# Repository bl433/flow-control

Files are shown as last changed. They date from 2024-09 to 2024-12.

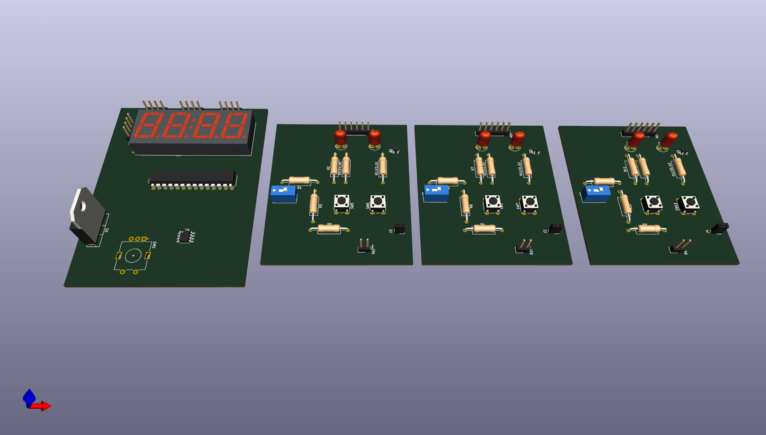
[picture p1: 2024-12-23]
hardware/kicad/flowcontrol_render.png

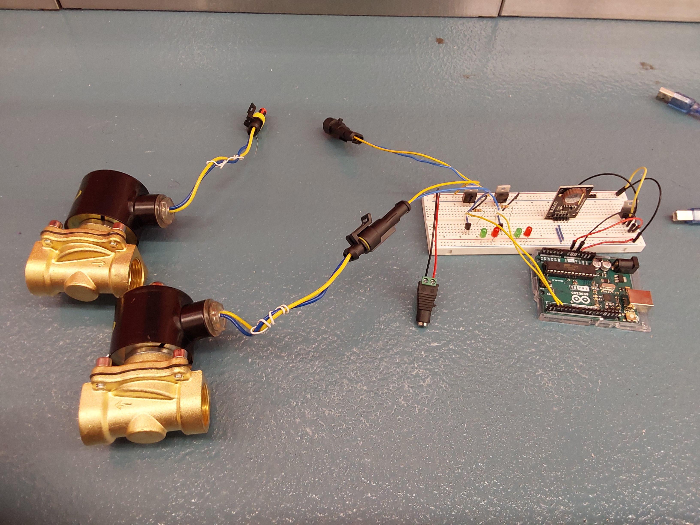
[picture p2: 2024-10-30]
documentation/Breadboarding.jpg

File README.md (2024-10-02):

# flow-control
Solenoid valve manager with PWM-styled energizing, master control, and possible flow rate feedback.
- Nozzle sizes are 3/4", meant for standard purpose garden hoses.
- Intended to be powered by a 12V 2A power supply.
- Solenoids are connected to the bottom of the valve manager through a 2-pin socket.

<b>This repository is intended for the NJIT ECET-430 course.</b>

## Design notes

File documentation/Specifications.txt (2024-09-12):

Suggested components:
 - resistors
 - MOSFET transistors or relays
 - indicator LEDs
 - 5V voltage regulators

Main Switch:
 - single-pole, single-throw
 - final decision: entire solenoid valve is off if this is off

Potentiometer Knob:
 - turnable, variable resistor
 - delays the solenoid valve for a variable amount of hours depending how far the potentiometer turns
 - solenoid valve is allowed a specific duty cycle to conserve water
 - turning the knob at maximum should allow the solenoid to open every 24 hours,
 - while turning the knob at minimum should allow the solenoid to open every 1 hours.
 - another knob can be used to decide how LONG the solenoid valve opens.

Solenoid Valve:
 - handles liquid transfer based on Main Switch ~~and Potentiometer Knob~~
 - 3/4in diameter
 - 12V, 2A input
 ~ 30 min active time until it begins to overheat

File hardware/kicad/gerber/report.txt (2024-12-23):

Warning: Width correction constrained.  The width correction value must be in the range of [0.000001 mm; 0.199999 mm] for the current design rules.
Plotted to 'H:\GitHub\flow-control\hardware\kicad\gerber\flowcontrol_BL-F_Cu.gbr'.
Plotted to 'H:\GitHub\flow-control\hardware\kicad\gerber\flowcontrol_BL-In1_Cu.gbr'.
Plotted to 'H:\GitHub\flow-control\hardware\kicad\gerber\flowcontrol_BL-In2_Cu.gbr'.
Plotted to 'H:\GitHub\flow-control\hardware\kicad\gerber\flowcontrol_BL-B_Cu.gbr'.
Plotted to 'H:\GitHub\flow-control\hardware\kicad\gerber\flowcontrol_BL-F_Paste.gbr'.
Plotted to 'H:\GitHub\flow-control\hardware\kicad\gerber\flowcontrol_BL-B_Paste.gbr'.
Plotted to 'H:\GitHub\flow-control\hardware\kicad\gerber\flowcontrol_BL-F_Silkscreen.gbr'.
Plotted to 'H:\GitHub\flow-control\hardware\kicad\gerber\flowcontrol_BL-B_Silkscreen.gbr'.
Plotted to 'H:\GitHub\flow-control\hardware\kicad\gerber\flowcontrol_BL-F_Mask.gbr'.
Plotted to 'H:\GitHub\flow-control\hardware\kicad\gerber\flowcontrol_BL-B_Mask.gbr'.
Plotted to 'H:\GitHub\flow-control\hardware\kicad\gerber\flowcontrol_BL-Edge_Cuts.gbr'.
Created Gerber job file 'H:\GitHub\flow-control\hardware\kicad\gerber\flowcontrol_BL-job.gbrjob'.
Info: Done.

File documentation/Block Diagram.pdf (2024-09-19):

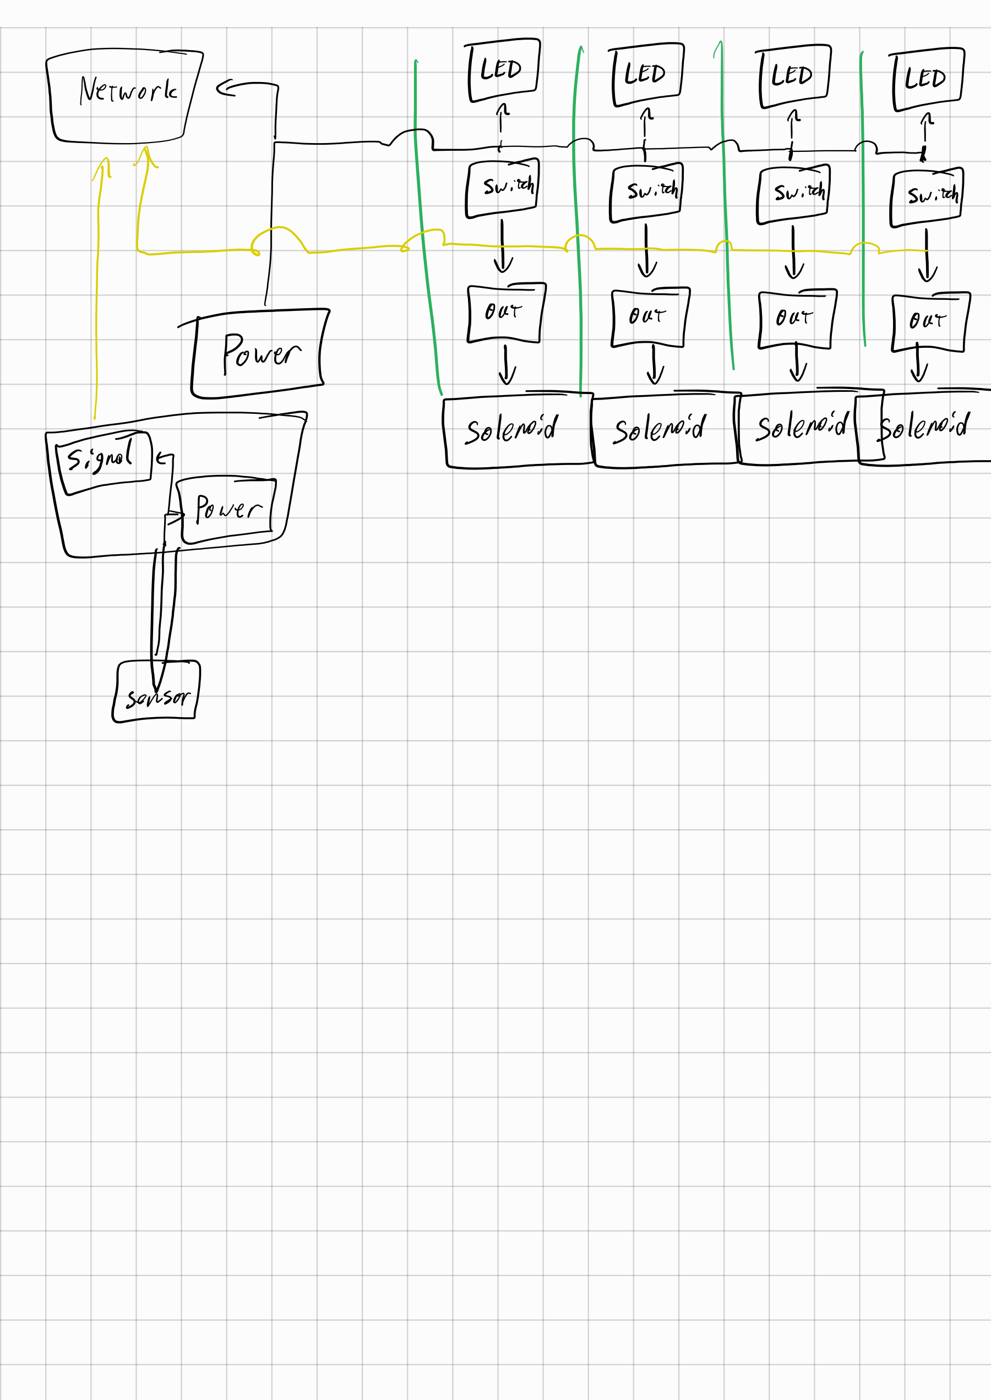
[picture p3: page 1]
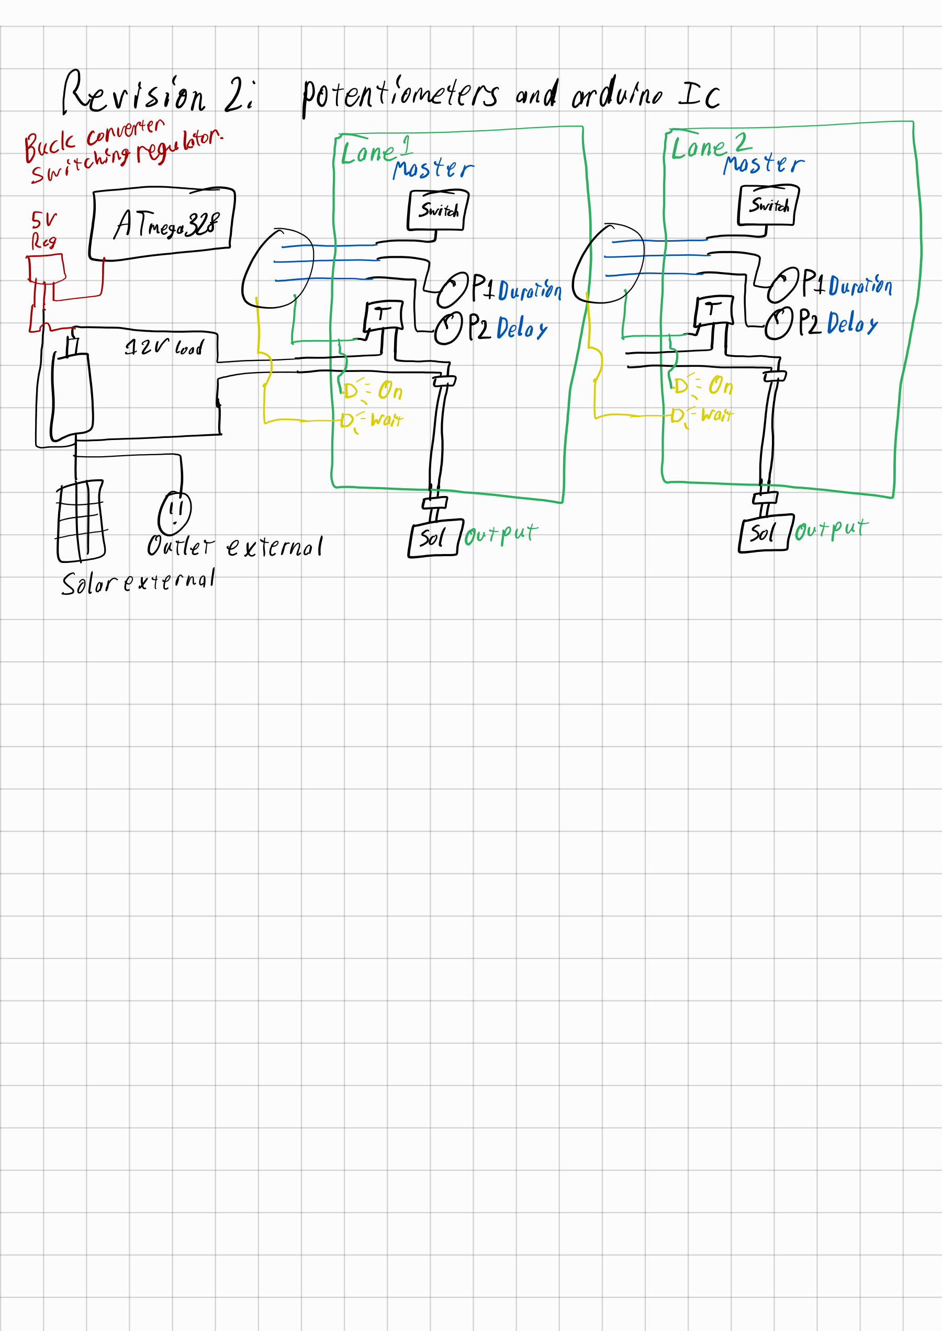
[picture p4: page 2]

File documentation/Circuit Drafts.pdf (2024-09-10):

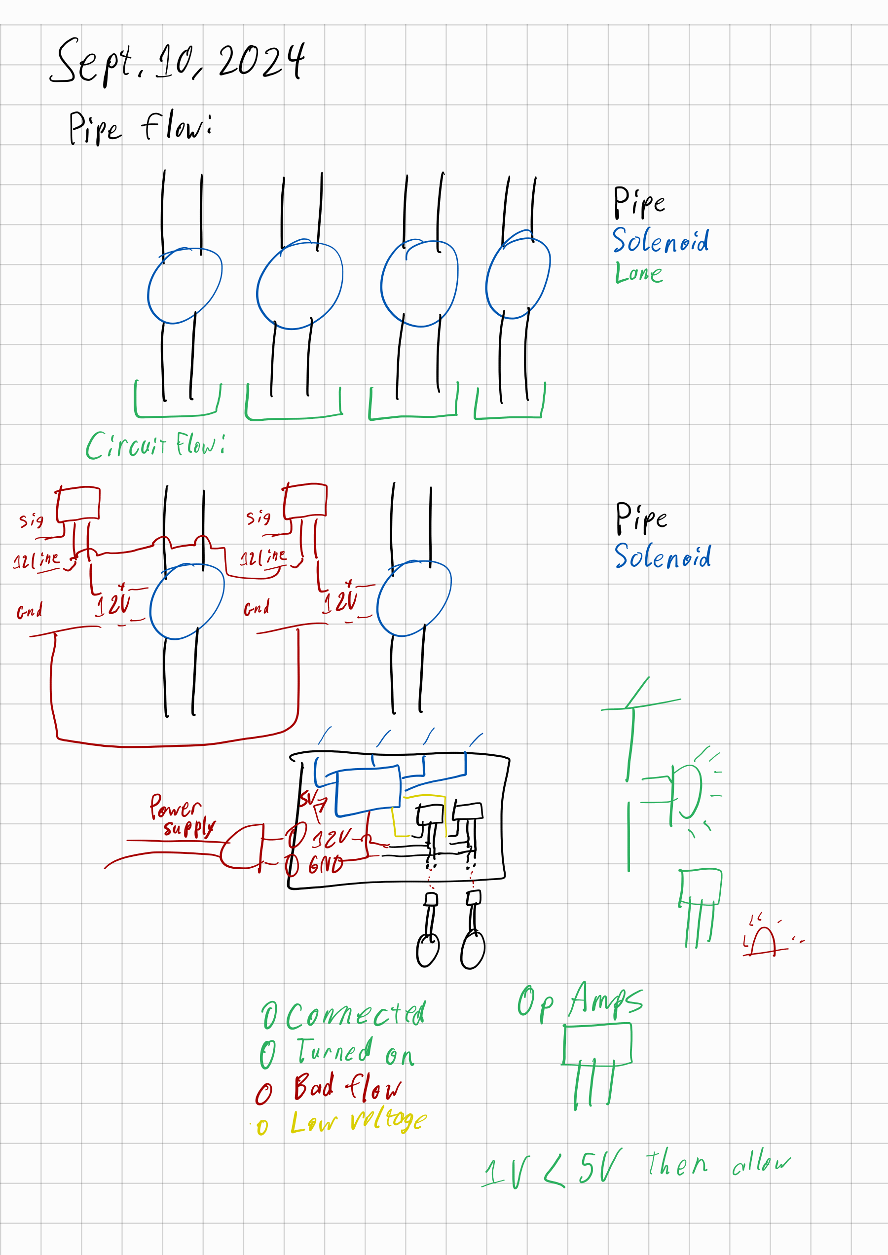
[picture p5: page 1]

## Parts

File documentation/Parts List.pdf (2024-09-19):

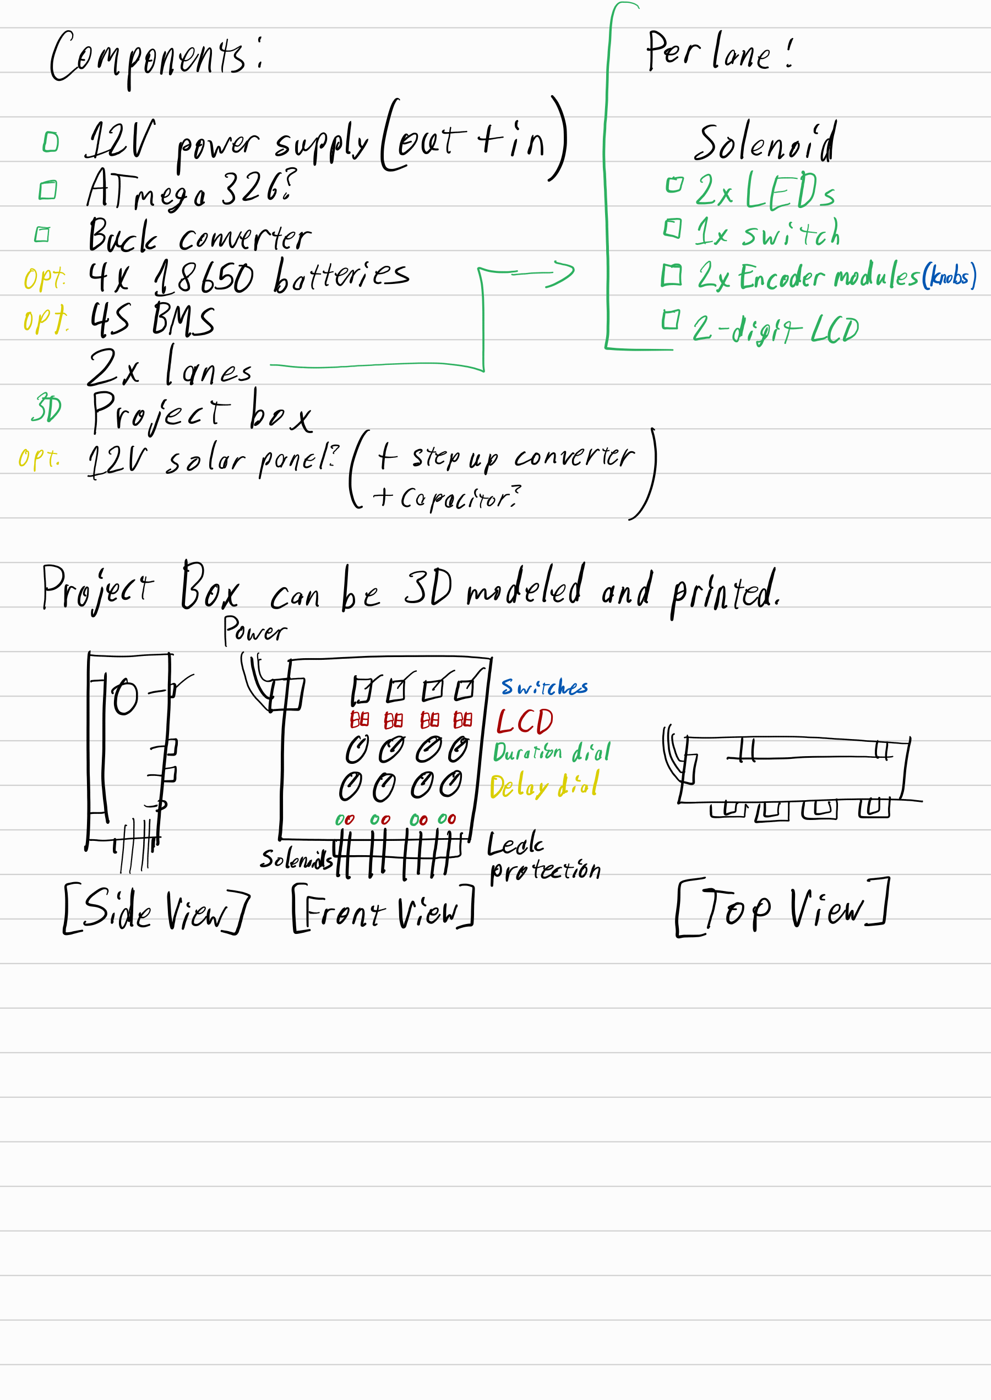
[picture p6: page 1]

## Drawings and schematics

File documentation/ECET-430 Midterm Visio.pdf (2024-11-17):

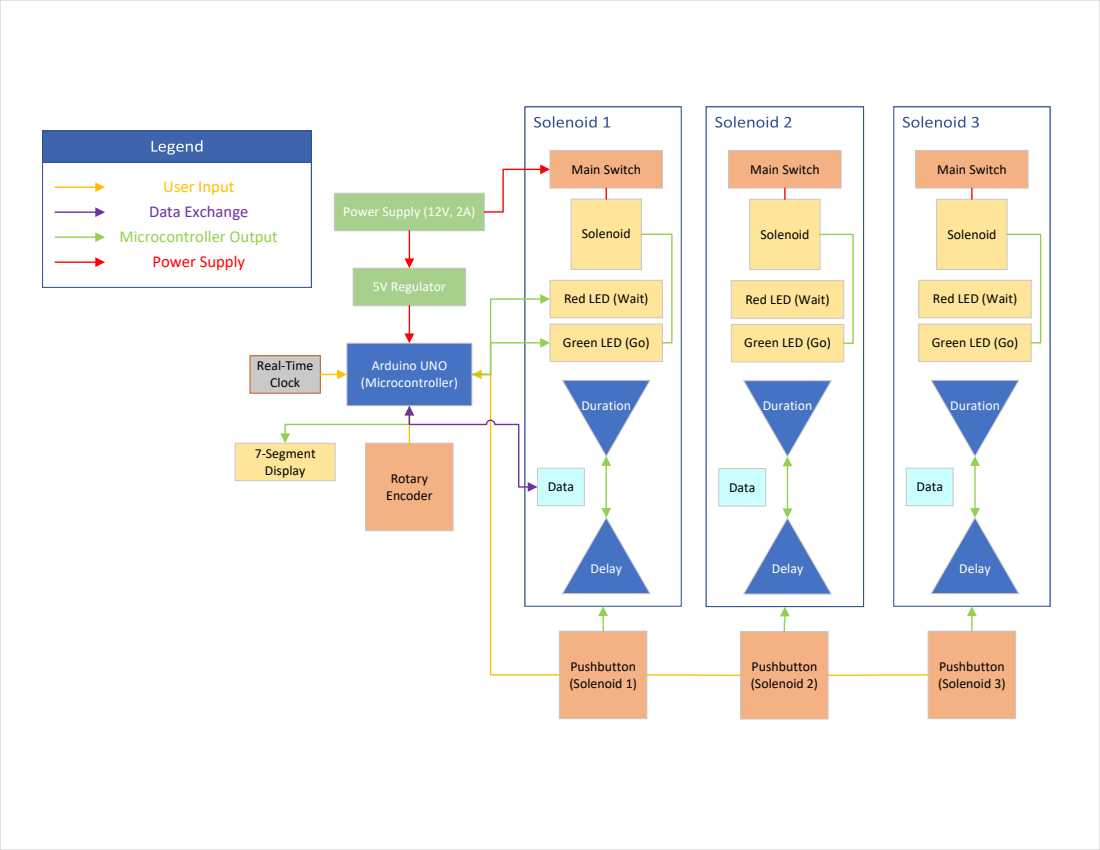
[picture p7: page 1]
Power Supply (12V, 2A); Arduino UNO (Microcontroller); Pushbutton (Solenoid 1); Delay; Duration; Rotary Encoder; Solenoid; 5V Regulator; 7-Segment Display; Data; Real-Time Clock; Pushbutton (Solenoid 2); Pushbutton (Solenoid 3); User Input Data Exchange; Microcontroller Output; Power Supply; Main Switch

Red LED (Wait)

Green LED (Go)

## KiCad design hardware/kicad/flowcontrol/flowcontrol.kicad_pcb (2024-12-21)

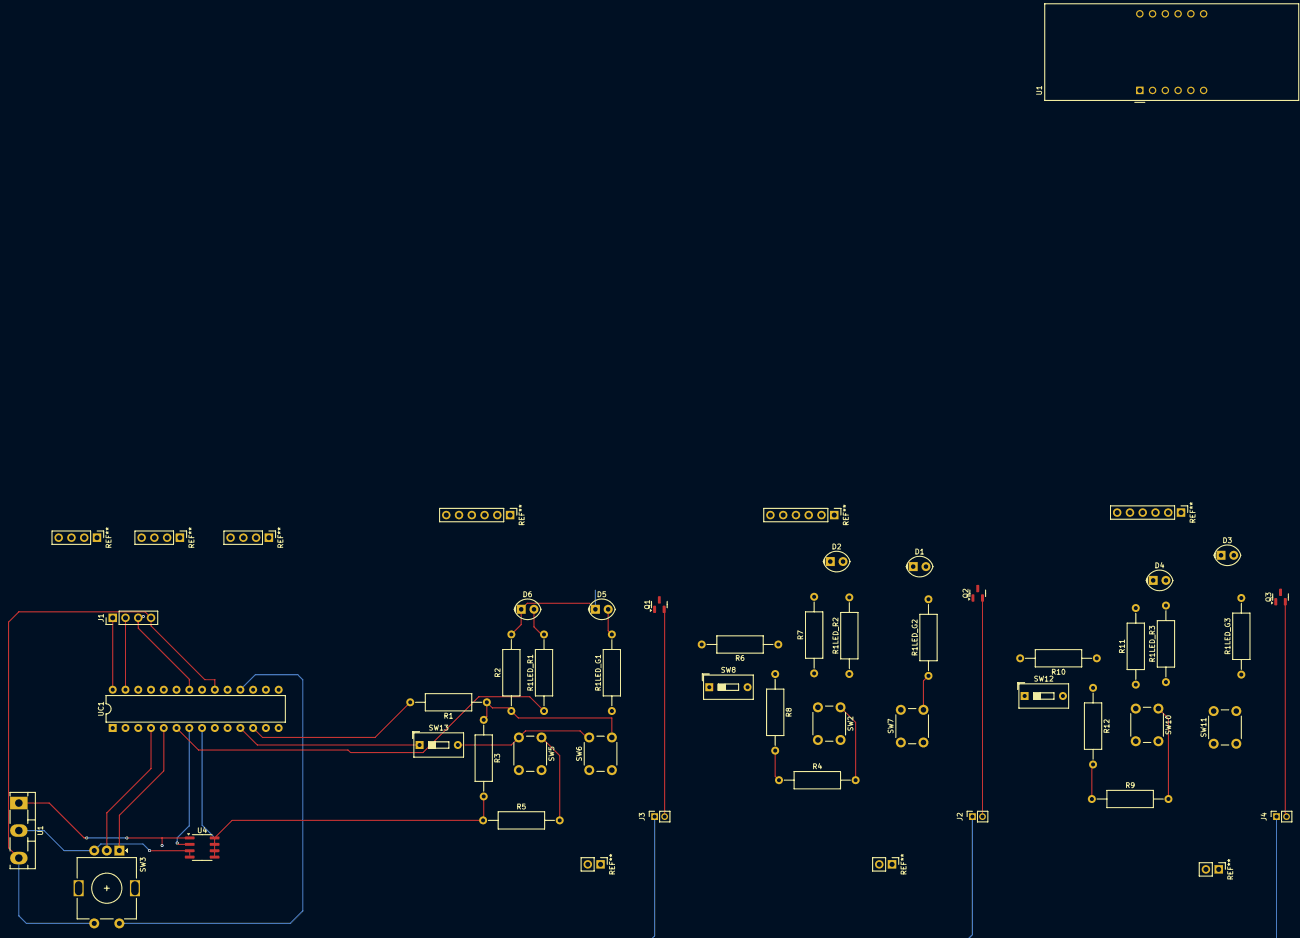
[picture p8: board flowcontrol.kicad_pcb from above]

Board: 2 copper layers, 45 parts (0 on the bottom side), 33 nets.

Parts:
D1, D3, D5: SOL1_GRN; LED_Oval_W5.2mm_H3.8mm
D2, D4, D6: SOL1_RED; LED_Oval_W5.2mm_H3.8mm
J1: 4-digit I2C Display; PinHeader_1x04_P2.54mm_Vertical
J2, J3, J4: SOL1_PORT; PinSocket_1x02_P2.00mm_Vertical
Q1, Q2, Q3: SOL1_NFET; SOT-23
R1, R6, R10: 100O; R_Axial_DIN0309_L9.0mm_D3.2mm_P15.24mm_Horizontal
R1LED_G1, R1LED_G2, R1LED_G3: 220; R_Axial_DIN0309_L9.0mm_D3.2mm_P15.24mm_Horizontal
R1LED_R1, R1LED_R2, R1LED_R3: R; R_Axial_DIN0309_L9.0mm_D3.2mm_P15.24mm_Horizontal
R2, R4, R5, R7, R9, R11: 1kO; R_Axial_DIN0309_L9.0mm_D3.2mm_P15.24mm_Horizontal
R3, R8, R12: 100; R_Axial_DIN0309_L9.0mm_D3.2mm_P15.24mm_Horizontal
SW2, SW5, SW10: BUTTON_CONFIG; SW_PUSH_6mm_mod
SW3: DIAL; RotaryEncoder_Vertical_H20mm
SW6, SW7, SW11: BUTTON_FORCE; SW_PUSH_6mm_mod
SW8, SW12, SW13: SWITCH_MAIN; SW_DIP_SPSTx01_Slide_9.78x4.72mm_W7.62mm_P2.54mm
U1: SOL1_DISP; CA56-12SRWA
U1#2: 5V Regulator; TO-218-3_Vertical
U4: XL1509-3.3; SOIC-8_3.9x4.9mm_P1.27mm
UC1: ATmega328-P; DIP-28_W7.62mm

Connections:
/Input Display/12V_R: J2.1, J3.1, J4.1, U1#2.1 (IN), U4.1 (VIN)
/Input Display/CLOCK: SW3.C, UC1.4 (PD2)
/Input Display/DT: SW3.A, UC1.5 (PD3)
/Input Display/SCL: J1.1, UC1.28 (PC5)
/Input Display/SDA: J1.2, UC1.27 (PC4)
/Input Display/SWITCH: SW3.S2, UC1.18 (PB4)
/Input Display/VCC_E: J1.4, SW2.4, SW3.S1, SW5.4, SW6.1, SW7.1, SW8.2 (B), SW10.4, SW11.1, SW12.2 (B), SW13.2 (B), U1#2.3 (OUT), UC1.20 (AVCC)
/Microcontroller/SOL1_MAIN: SW13.1 (A), UC1.11 (PD5)
/Microcontroller/SOL1_OUT: R1.2, UC1.12 (PD6)
/Microcontroller/SOL1_SEL: R5.2, SW5.3, UC1.13 (PD7)
/Microcontroller/SOL1_WAIT: R1LED_R1.1, UC1.6 (PD4)
/Microcontroller/SOL2_MAIN: SW8.1 (A), UC1.14 (PB0)
/Microcontroller/SOL2_OUT: R6.2, UC1.15 (PB1)
/Microcontroller/SOL2_SEL: R4.2, SW2.3, UC1.17 (PB3)
/Microcontroller/SOL2_WAIT: R1LED_R2.1, UC1.16 (PB2)
/Microcontroller/SOL3_MAIN: SW12.1 (A), UC1.23 (PC0)
/Microcontroller/SOL3_OUT: R10.2, UC1.24 (PC1)
/Microcontroller/SOL3_SEL: R9.2, SW10.3, UC1.26 (PC3)
/Microcontroller/SOL3_WAIT: R1LED_R3.1, UC1.25 (PC2)
GND: D1.1 (K), D2.1 (K), D3.1 (K), D4.1 (K), D5.1 (K), D6.1 (K), J1.3, Q1.1 (D), Q1.3 (G), Q2.1 (D), Q2.3 (G), Q3.1 (D), Q3.3 (G), R2.2, R3.2, R4.1, R5.1, R7.2, R8.2, R9.1, R11.2, R12.2, SW3.B, U1#2.2 (GND), U4.3 (FB), U4.4 (~EN), U4.5 (GND), U4.6 (GND), U4.7 (GND), U4.8 (GND), UC1.8 (GND), UC1.22 (GND)
unnamed: D1.2 (A), R1LED_G2.2
unnamed: D2.2 (A), R1LED_R2.2
unnamed: D3.2 (A), R1LED_G3.2
unnamed: D4.2 (A), R1LED_R3.2
unnamed: D5.2 (A), R1LED_G1.2
unnamed: D6.2 (A), R1LED_R1.2
unnamed: J2.2, Q2.2 (S)
unnamed: J3.2, Q1.2 (S)
unnamed: J4.2, Q3.2 (S)
unnamed: R1.1, R1LED_G1.1, R2.1, R3.1, SW6.2
unnamed: R1LED_G2.1, R6.1, R7.1, R8.1, SW7.2
unnamed: R1LED_G3.1, R10.1, R11.1, R12.1, SW11.2
unnamed: U4.2 (OUT), UC1.7 (VCC)

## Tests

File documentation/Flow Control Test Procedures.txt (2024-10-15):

Bruce Le's Test Procedures for the Flow Control manager [October 15th, 2024]:

 [Startup process:]
  - The product is energized as soon as it's plugged in. To ensure the product is working afterwards, it should light up all the RED (delay) LEDs for a few seconds.
  - The purpose of this test is to verify that the product will work as intended with some kind of "sanity test." If it does not have its LEDs light up for a few seconds, then its instructions were incorrectly uploaded, or some components may have failed.

 [Manual activation:]
  - Press the duration encoder knob to manually enable the solenoid, independent of the cycle.
  - This can be ideal for sampling where the water will go when connecting it to a pipe network.
  - The purpose of this test is to verify that the solenoids themselves are working as intended, meaning the solenoids can activate as intended when the delay cycle passes.

 [Template activation cycle:]
  - A small-scale test instance. On a duration of 30 seconds, and a delay of 60 seconds, the solenoid should wait 60 seconds before opening for 30 seconds. This cycle must constantly repeat.
  - During this time, the red LED must be blinking, showing that the solenoid is currently on its delay cycle, then the green LED must be solid for 30 seconds, showing that it's then on an active cycle.
  - The purpose of this test is to verify that the delay and duration cycles work to the user's intent. The duration and delay timers can be increased until it can be considered comfortable to perform a 10-hour delay or greater.

 [Adjusting individual settings:]
  - Each of the two encoder knobs can be turned to change the settings for the respective solenoid. The settings must be independent for each solenoid.
   [IE. Solenoid 1 has a duration of 5 minutes 05:00 and a delay of 20 hours 20:00
        Solenoid 2 has a duration of 10 minutes 10:00 and a delay of 12 hours 12:00]
  - The purpose of this test is to verify that each solenoid will have their own individual settings, as well as opening and closing at different intervals as per the solenoid's provided duration and delay.
  - A solenoid should not follow the duration or delay that is assigned to another solenoid.

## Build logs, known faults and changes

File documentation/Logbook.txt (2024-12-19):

flow-control (12V, 2A each) logbook [Fall Semester, 2024]
Bruce Le, mohammad, Felipe
September 3rd, 2024
 - Initiated project, proposed solenoid valve manager
 - Placed order for two solenoid valves
 - Set up github directories
September 5th, 2024
 - Sorted github directories
<<<<<<< HEAD
September 10th, 2024
 - Drawn block diagram and circuit drafts
 - Changed up specifications
  - Changed from partially open solenoid valves to cyclically open solenoid valves
September 12th, 2024
 - Decided to integrate Arduino
  - Requires the Arduino code and USB to serial conversion
=======
September 12th, 2024
 - Added parts list

=======
October 17th, 2024
 - Test operated solenoids through an Arduino blink function
October 28th, 2024
 - Assembled solderless breadboard circuit and installed waterproof cables for solenoids
November 13th, 2024
- Test out the project's functions prior to the presentation midterm.
December 12th, 2024
- Worked on the module board and mother board. Soldered them to be ready to present on 12/19.

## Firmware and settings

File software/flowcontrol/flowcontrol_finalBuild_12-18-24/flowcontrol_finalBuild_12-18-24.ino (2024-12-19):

/* ECET-430 Midterm - Flow Control Prototype
  We want this to exhibit the basics of what we're doing.
  Eventually we'll evolve this to two solenoids, but three and four is a pipe dream unless we can expand the IO pins.
  Each solenoid will be backed with a master switch.
  
*/

//================//
// PIN DEFINITION //
//================//

// Define rotary encoder pins
#define ENC_A 2
#define ENC_B 3
#define ENC_SW 12
// MAIN - Main decision switch. Solenoid will not flow or count down if not receiving 5v. (off)
// OUT - Output valve control. Linked to the green LED.
// WAIT - Hold visual. Linked to the red LED.
// SW_SEL - Pushbutton to select solenoid for configuration. Push once for Delay, push twice for Duration.
// SW_FORCE - Pushbutton to forcefully enable SOL1_OUT. This doesn't even need to exist and can be linked to a 5V.
#define SOL1_MAIN 5
#define SOL1_OUT 6
#define SOL1_WAIT 4
#define SOL1_SW_SEL 7
//#define SOL1_SW_FORCE 11
#define SOL2_MAIN 8
#define SOL2_OUT 9
#define SOL2_WAIT 10
#define SOL2_SW_SEL 11
// It's impossible to expand to the fourth solenoid with the current microcontroller unless there's a way to expand the pins.
// We COULD squeeze one, pins 14, 15, 16, 17 for SOL3. Not SOL4 though. Three might as well be our absolute maximum.
// There are ways. An 8-pin expansion board would be ideal for this matter, but ends up relying on I2C communications, SDA, and SCL.
#define SOL3_MAIN 14
#define SOL3_OUT 15
#define SOL3_WAIT 16
#define SOL3_SW_SEL 17

#define HOUR_CONVERT 60
#include "HT16K33.h"

unsigned long _lastIncReadTime = micros(); 
unsigned long _lastDecReadTime = micros(); 
int _pauseLength = 25000;
int _fastIncrement = 10;
int _delaysPerSecond = 10;
int delayCount = 0;
#define ONE_SECOND 1000

//======================//
// VARIABLE DEFINITIONS //
//======================//

// Solenoids based on the manual switch. MUST default to false if the switch is damaged.
bool solenoidEnabled[] = {false, false, false};
// Solenoids with individual duration counters, in seconds.
int solenoidDuration[] = {0, 0, 0};
// Solenoids with individual delay counters, in minutes.
// Neither the delay or duration counters can go below 0.
int solenoidDelay[] = {1, 2, 3};
// Current solenoid. Ranges from 1 to 3.
int solenoidSelect = 1;
// Editing what part of that solenoid. 1 for delay, 2 for duration.
int solenoidEditing = 1;
// Counters. These go down one for every minute.
//  They'd be normally what, 60, 120, 180 minutes? Setting these to 1, 2, and 3 is just for the presentation tomorrow.
int solenoidCounters[] = {1, 2, 3};
int secondCounter = 0;
int blinkState = LOW;

struct HrAndMin {
  int16_t hours;
  int16_t minutes;
};

// Constraints - if the counters ever go past these numbers, the code will force the value to the cap values.
#define SOL_MAX 1800
#define SOL_MIN 0

// This counter will be useful. Basically when you select a solenoid...
//  LOAD the DELAY to the COUNTER and UPDATE the value.
//  Make it display DELAY (DEly) for a second, then the actual counter itself.
//  Adjust the COUNTER to what you desire.
//  Press the encoder switch to SAVE the COUNTER to the DELAY.
//  Make the LCD say SET or something.
// Same goes if you press the select button again to select the solenoid's duration.

volatile int16_t counter = 0;
HT16K33 seg(0x70);

// Setup is to set all the variables and pins.
void setup();
// Loop is to consistently check and adjust values.
void loop();
// Switch is to identify what solenoid we're going to adjust.
void solenoid_switch(int ID);
// Duration can never go below 0.
int solenoid_flow(int ID, int duration);
// Included for the encoder module.
void read_encoder();
// Not included for the encoder module. Summarizes all things in the loop to this.
void dial_encoder(int newValue);
// Not included for the encoder module, but we'll want it to perform a saving action.
void press_encoder();
// Every second that passes, run a step up, and check if that step goes past any of the set counters.
// And when that happens, flow.
void proc_second();
void check_mains();
// We'll translate the raw counter numbers into hours, minutes, and seconds.
// This one function is double-purposed since if the value is in seconds, it'll be MMSS anyway.
int16_t base10ToHHMM();
// Displays a custom text line, like SET, Dura, DEly,
void displayText(uint8_t first, uint8_t second, uint8_t third, uint8_t fourth, int duration);
void display10ToHHMM(int value);

void setup() {
  // Start the serial monitor to show output
  Serial.begin(115200);
  // Set encoder pins and attach interrupts
  // Encoder knob
  pinMode(ENC_A, INPUT_PULLUP);
  pinMode(ENC_B, INPUT_PULLUP);
  pinMode(ENC_SW, INPUT_PULLUP);
  
  attachInterrupt(digitalPinToInterrupt(ENC_A), read_encoder, CHANGE);
  attachInterrupt(digitalPinToInterrupt(ENC_B), read_encoder, CHANGE);

  // Set up solenoid modules - comment out some if needed.
  // First solenoid
  pinMode(SOL1_MAIN, INPUT);
  pinMode(SOL1_OUT, OUTPUT);
  pinMode(SOL1_WAIT, OUTPUT);
  pinMode(SOL1_SW_SEL, INPUT);
  // Second solenoid
  pinMode(SOL2_MAIN, INPUT);
  pinMode(SOL2_OUT, OUTPUT);
  pinMode(SOL2_WAIT, OUTPUT);
  pinMode(SOL2_SW_SEL, INPUT);
  // Third solenoid
  pinMode(SOL3_MAIN, INPUT);
  pinMode(SOL3_OUT, OUTPUT);
  pinMode(SOL3_WAIT, OUTPUT);
  pinMode(SOL3_SW_SEL, INPUT);

  // Set up counter
  Wire.begin();
  Wire.setClock(100000);
  seg.begin();

  // Set up segment display
  seg.displayOn();
  seg.setBrightness(2);
  seg.displayClear();
  seg.setBlink(0);
  seg.setDigits(1);

  // Initial setup of the delay values.
  for(int i = 0; i < 3; i++)
    solenoidCounters[i] = solenoidDelay[i];
  
  digitalWrite(SOL1_WAIT, LOW);
  digitalWrite(SOL2_WAIT, LOW);
  digitalWrite(SOL3_WAIT, LOW);
  delay(1000);
}

void loop() {
  delay(ONE_SECOND / _delaysPerSecond);
  delayCount++;
  check_mains();
  if(delayCount >= _delaysPerSecond)
    proc_second();

  static int lastCounter = 0;
  // If count has changed print the new value to serial
  if(counter != lastCounter)
  {
    lastCounter = counter;
    dial_encoder(counter);
  }
  
  // Pressing any of the switch buttons. NOT the force button.
  if (digitalRead(SOL1_SW_SEL) == HIGH || digitalRead(SOL2_SW_SEL) == HIGH || digitalRead(SOL3_SW_SEL) == HIGH)
    solenoid_switch(digitalRead(SOL1_SW_SEL) == HIGH ? 0 : (digitalRead(SOL2_SW_SEL) == HIGH ? 1 : 2));
  
  // Pressing the encoder button, which will SET the counter's value to the database.
  if (digitalRead(ENC_SW) == LOW)
    press_encoder();

  // The force buttons are hardcoded. Please don't press two of them at once. Each solenoid runs on TWO AMPS and twelve volts.
  //  Those MOSFETs heat up real fast even for its thirty-amp capacity, and I got a half-a-degree burn on my finger demonstrating it.
  //  Either I'm wiring it up wrong, or it's just how two amps is. AT least the MOSFET isn't heating while it's idle.
  
  
}

void proc_second()
{
  delayCount = 0;
  secondCounter++;
  
  Serial.print("Seconds: ");
  Serial.println(secondCounter);
  // Switch states.
  //blinkState
  if (blinkState == HIGH)
    blinkState = LOW;
  else
    blinkState = HIGH;

  if (secondCounter < HOUR_CONVERT)
    return;
  // If the second counter reaches 60 (counts from 0 to 59, 60 >= 60), then the following below gets run.
  // Reset the seconds before anything else.
  secondCounter = 0;
  for(int i = 0; i < 3; i++)
  {
    solenoidCounters[i]--;
    Serial.println(solenoidCounters[i]);
    if (solenoidCounters[i] == 0)
    {
      // Flow it. The code won't continue due to the duration.
      solenoid_flow(i, solenoidDuration[i]);
      // Reset the counter.
      solenoidCounters[i] = solenoidDelay[i];
    }
  }
  
}

// Checks for each switch. If it's reading high, then the solenoid is enabled.
void check_mains()
{
  digitalWrite(SOL1_WAIT, (digitalRead(SOL1_MAIN) == LOW ? LOW : blinkState));
  digitalWrite(SOL2_WAIT, (digitalRead(SOL2_MAIN) == LOW ? LOW : blinkState));
  digitalWrite(SOL3_WAIT, (digitalRead(SOL3_MAIN) == LOW ? LOW : blinkState));
  // check every tick.
  // but also blink the red light every second's worth of ticks.

}

int solenoid_flow(int ID, int duration)
{
  Serial.print("Flowing ");
  Serial.println(ID);
  switch(ID)
  {
    case 0:
      if (digitalRead(SOL1_MAIN) == LOW)
        return;
      digitalWrite(SOL1_OUT, HIGH); digitalWrite(SOL1_WAIT, LOW); break;
    case 1:
      if (digitalRead(SOL2_MAIN) == LOW)
        return;
      digitalWrite(SOL2_OUT, HIGH); digitalWrite(SOL2_WAIT, LOW); break;
    case 2:
      if (digitalRead(SOL3_MAIN) == LOW)
        return;
      digitalWrite(SOL3_OUT, HIGH); digitalWrite(SOL3_WAIT, LOW); break;
  }
  delay(duration * 1000);
  digitalWrite(SOL1_OUT, LOW);
  digitalWrite(SOL2_OUT, LOW);
  digitalWrite(SOL3_OUT, LOW);
  return;
}

// Press the encoder and set the value to the database.
//  There's two arrays: delay and duration, split to three containers, one per solenoid.
void press_encoder(){
  Serial.println(counter);
  switch(solenoidEditing)
  {
    case 1: solenoidDelay[solenoidSelect] = counter; solenoidCounters[solenoidSelect] = counter; break;
    case 2: solenoidDuration[solenoidSelect] = counter; break;
    default: displayText(SEG_A, SEG_A, SEG_A, SEG_NONE, 2.0f); return;
  }
  // print SEt for 2.5s
  displayText(SEG_A | SEG_F | SEG_G | SEG_C | SEG_D, SEG_A | SEG_D | SEG_E | SEG_F | SEG_G, SEG_F | SEG_E | SEG_G | SEG_D, SEG_NONE, 2.0f);
}

// Dial the encoder and change the counter value.
//  At the same time, let the user know how high they're setting the counter.
void dial_encoder(int newValue) {
    //counter = newValue;
    //lastCounter = counter;
    display10ToHHMM(counter);
    Serial.println(counter);
}

void solenoid_switch(int ID){
  // If it's the same switch, switch between delay and duration. The second press leads to the selected solenoid's duration.
  if(solenoidSelect == ID)
  {
    solenoidEditing = (solenoidEditing == 1 ? 2 : 1);
    Serial.print("Switched between delay and duration: ");
    Serial.println(solenoidEditing);
  }
  else
  {
    // Select the new solenoid, and load the values to the counter.
    solenoidSelect = ID;
    solenoidEditing = 1;
    
    Serial.println("Selecting different solenoid");
  }
  /*
    If 1: display dELy
     SEG_B | SEG_C | SEG_D | SEG_E | SEG_G
     SEG_A | SEG_D | SEG_E | SEG_F | SEG_G
     SEG_D | SEG_E | SEG_F
     SEG_B | SEG_C | SEG_D | SEG_F | SEG_G
    If 2: display durA
     SEG_B | SEG_C | SEG_D | SEG_E | SEG_G
     SEG_C | SEG_D | SEG_E
     SEG_E | SEG_G
     SEG_A | SEG_B | SEG_C | SEG_E | SEG_F | SEG_G
  */
  if(solenoidEditing == 1)
  {
    counter = solenoidDelay[solenoidSelect];
    displayText(SEG_B | SEG_C | SEG_D | SEG_E | SEG_G, SEG_A | SEG_D | SEG_E | SEG_F | SEG_G, SEG_D | SEG_E | SEG_F, SEG_B | SEG_C | SEG_D | SEG_F | SEG_G, 2.0f);
  }
  else
  {
    counter = solenoidDuration[solenoidSelect];
    displayText(SEG_B | SEG_C | SEG_D | SEG_E | SEG_G, SEG_C | SEG_D | SEG_E, SEG_E | SEG_G, SEG_A | SEG_B | SEG_C | SEG_E | SEG_F | SEG_G, 2.0f);
  }
}

void read_encoder() {
  // Encoder interrupt routine for both pins. Updates counter
  // if they are valid and have rotated a full indent
 
  static uint8_t old_AB = 3;  // Lookup table index
  static int8_t encval = 0;   // Encoder value  
  static const int8_t enc_states[]  = {0,-1,1,0,1,0,0,-1,-1,0,0,1,0,1,-1,0}; // Lookup table

  old_AB <<=2;  // Remember previous state

  if (digitalRead(ENC_A)) old_AB |= 0x02; // Add current state of pin A
  if (digitalRead(ENC_B)) old_AB |= 0x01; // Add current state of pin B
  
  encval += enc_states[( old_AB & 0x0f )];

  // Update counter if encoder has rotated a full indent, that is at least 4 steps
  if( encval > 3 ) {        // Four steps forward
    int changevalue = 1;
    if((micros() - _lastIncReadTime) < _pauseLength) {
      changevalue = _fastIncrement * changevalue; 
    }
    _lastIncReadTime = micros();
    counter = counter + changevalue;              // Update counter
    encval = 0;
  }
  else if( encval < -3 ) {        // Four steps backward
    int changevalue = -1;
    if((micros() - _lastDecReadTime) < _pauseLength) {
      changevalue = _fastIncrement * changevalue; 
    }
    _lastDecReadTime = micros();
    counter = counter + changevalue;              // Update counter
    encval = 0;
  }
  // The counter can never go below 0. Neither can it go above the max define.
  if (counter < SOL_MIN)
    counter = SOL_MIN;
  else if (counter > SOL_MAX)
    counter = SOL_MAX;
} 

// Base 10 to Hours:Minutes, take the value that's interpreted in minutes, and return it in a HH:MM format.
//  We can just put a bool of this and if it's true- or just not put it at all because the variables will just adjust itself.
HrAndMin base10ToHHMM(int16_t input)
{
  // Can be minutes if using a value that has seconds.
  //int hours = input / HOUR_CONVERT;
  // Can be seconds if using a value that has seconds.
  //int minutes = input % HOUR_CONVERT;
  //return {hours, minutes};
  return {input / HOUR_CONVERT, input % HOUR_CONVERT};
}

void displayText(uint8_t first, uint8_t second, uint8_t third, uint8_t fourth, float duration)
{
  // Suggestion: Prematurely cancel the delay if the knob is turned.
  uint8_t segment_data[] = {first, second, third, fourth};
  seg.displayClear();
  seg.displayColon(0);
  delay(100);
  seg.displayRaw(segment_data);
  delay(int(duration * 1000));
  seg.displayClear();
  delay(100);
  seg.displayInt(counter);
}

void display10ToHHMM(int value)
{
  seg.displayColon(1);
  HrAndMin toDisplay = base10ToHHMM(value);
  //int16_t toHours = toDisplay.hours;
  //int16_t toMinutes = toDisplay.minutes;
  seg.displayTime(toDisplay.hours, toDisplay.minutes, true, false);
}

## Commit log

2024-09-03 Update solenoid valves.txt
2024-09-05 Create .gitignore, kicad template
2024-09-12 september 12th
    Updated logs from September 10th
    Updated logs from September 12th
    Decided to integrate Arduino.
2024-09-16 replace block diagram
    added revision 2, featuring two sample lanes and two encoder module knobs per lane
2024-09-19 prepared kicad and arduino files
    Both files are very rudimentary. We'll eventually add psuedocode and fiddle with the components in the schematic so that we'll make these files proper.
    [flowcontrol.kicad_pcb, flowcontrol.kicad_sch]
2024-09-23 updated kicad file
    connected most devices together through labels.
    still requires LCD I2C modules or 4-digit schematic blocks.
    [flowcontrol.kicad_sch]
2024-10-02 KiCad Sectioning
    Turned the schematic into multiple sections - microcontroller, inputs, outputs, and display as the core blocks.
    [core_microcontrollers.kicad_sch, flowcontrol.kicad_sch, flowcontrol_sectionalized.kicad_sch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]
2024-10-15 Added requested test procedures
    Four ideal test protocols have been added:
    - Power-up sanity check
    - Manual activation
    - Small-scale interval
    - Individual settings
    [flowcontrol.kicad_sch]
2024-10-15 Update Flow Control Test Procedures.txt
2024-10-30 Schemiatic update
    [flowcontrol.kicad_pcb, flowcontrol.kicad_sch, sol1_inputs.kicad_sch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]
2024-11-14 Added Arduino coding
    [sol1_display.kicad_sch, sol1_inputs.kicad_sch, sol2_display.kicad_sch]
2024-11-14 Added Visio flowchart files
2024-12-19 Updated KiCad schematic to final rendition
    [core_microcontrollers.kicad_sch, flowcontrol.kicad_sch, sol1_inputs.kicad_sch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]
2024-12-19 labeled the old pcb old
    [core_microcontrollers.kicad_sch, flowcontrol.kicad_sch, flowcontrol_old.kicad_pcb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]
2024-12-21 semi-final updates for the report
    [core_microcontrollers.kicad_sch, flowcontrol.kicad_pcb, flowcontrol.kicad_sch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]
2024-12-23 finalized updates for the individual reports
    For the sake up uploading the ECET-430 final report before midnight. My variant is flowcontrol_BL, since you worked on the wiring as well.
    [flowcontrol_BL.kicad_pcb]
2024-12-23 Gerber, Drill, and Bill of Materials generation
    [flowcontrol_BL-B_Cu.gbr, flowcontrol_BL-B_Mask.gbr, flowcontrol_BL-B_Paste.gbr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]
